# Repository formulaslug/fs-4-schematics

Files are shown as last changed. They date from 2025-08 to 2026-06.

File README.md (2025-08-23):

# Notes

Please complete KiCad training before beginning or working on any projects in this repository.

Only edit another person's work if you have spoke about it with them first and they have given you permission. This applies to Leads and Captains as well.

Contact Cole Lewis, Nathaniel Platt, or Wesley Rodriguez Kronmiller or Jack Nystrom for information/help relating to this repository.

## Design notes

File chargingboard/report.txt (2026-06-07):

Plotted to '/Users/mihirb/Desktop/formula slug/chargingboard.pdf'.
Info: Done.
Plotted to '/Users/mihirb/Desktop/formula slug/chargingboard.pdf'.
Info: Done.
Info: Done.
Info: Done.

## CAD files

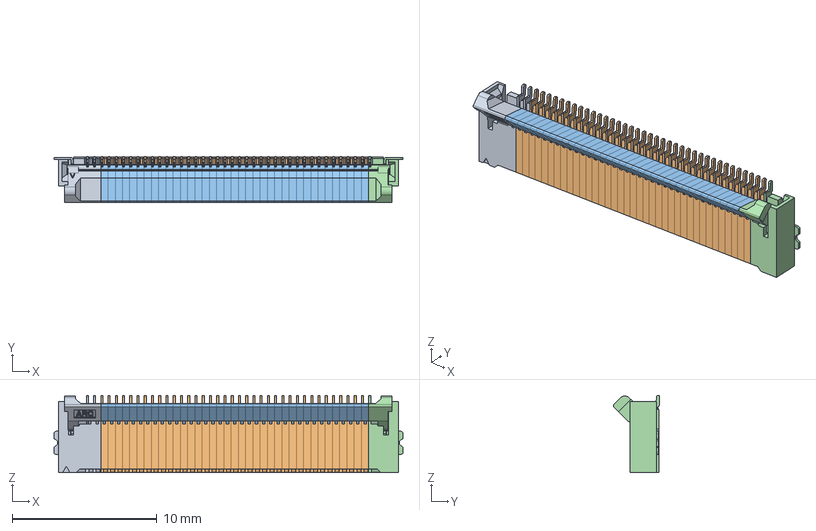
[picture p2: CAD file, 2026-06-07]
chargingboard/f32d_40pin_asm.stp
24.1 x 3.21 x 5.32 mm
F32D_L
F32D_M x 37
F32D_R

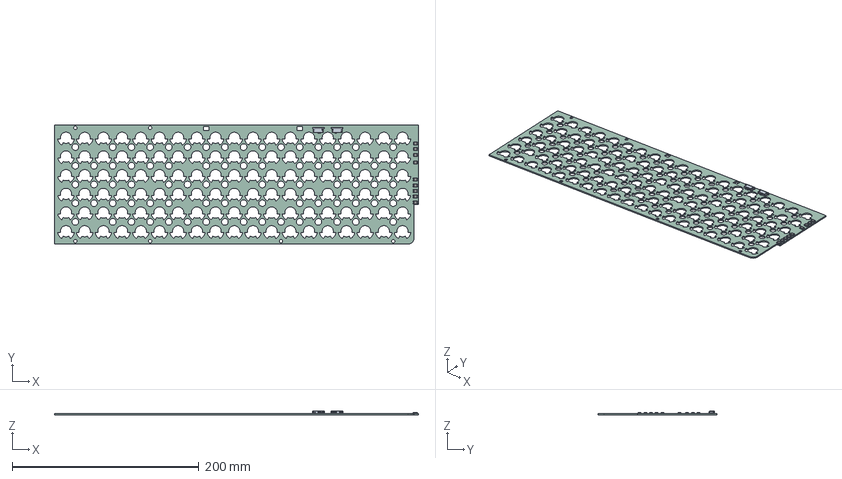
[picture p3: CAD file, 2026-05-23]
BMS Busbar Board/BMS Busbar Board/BMS Busbar Board.step
389.4 x 127.6 x 4.11 mm
1812L050_30PR x 9
BMS Busbar Board_PCB

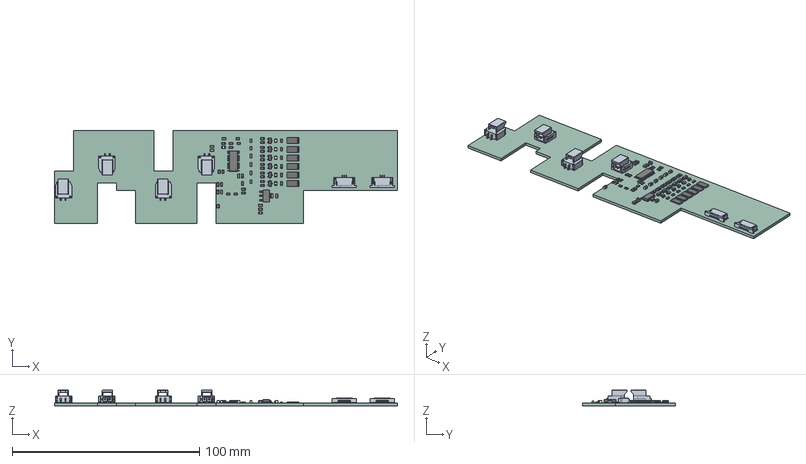
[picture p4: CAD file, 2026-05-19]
BMS/BMS/BMS.step
183.2 x 49.9 x 8.49 mm
R_0805_2012Metric x 35
C_0805_2012Metric x 14
LED_0805_2012Metric x 8
TSSOP-44_4.4x11mm_P0.5mm
R_2512_6332Metric x 6
SOT-223
SOT-23 x 6
BMS_PCB

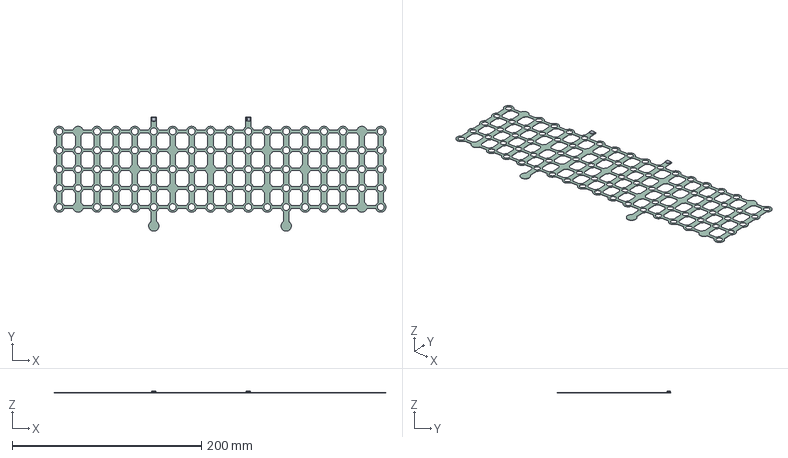
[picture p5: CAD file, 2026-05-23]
BMS/TempSenseBoard/TempSenseBoard.step
351.0 x 120.8 x 1.99 mm
TempSenseBoard_PCB

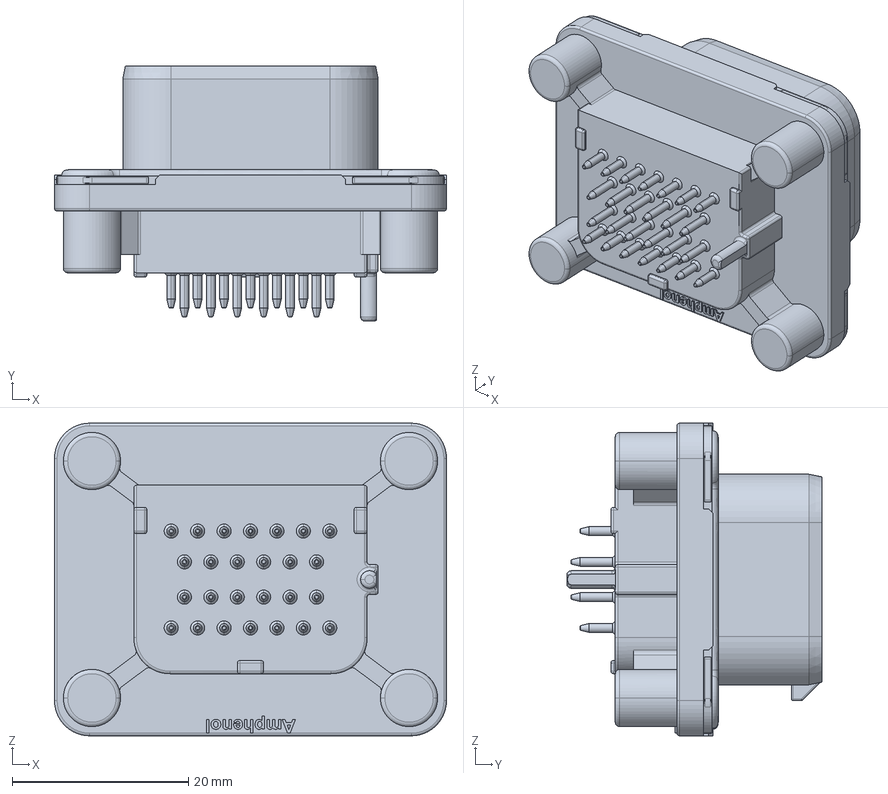
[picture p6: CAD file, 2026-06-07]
chargingboard/ATS15-26PB-BM01.stp
44.5 x 29.0 x 35.5 mm

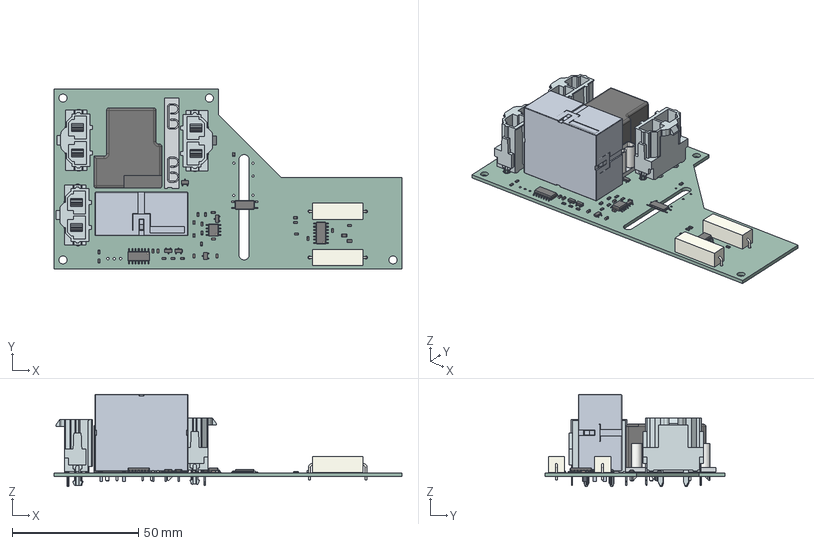
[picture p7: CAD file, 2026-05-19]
Power Electronics Board/Power Electronics Board.step
137.7 x 71.1 x 36.5 mm
SOIC-8_3.9x4.9mm_P1.27mm
TSOT-23 x 2
R_0603_1608Metric x 14
C_0603_1608Metric x 8
Pins
D_0603_1608Metric x 3
SOT-23-3 x 2
R_0805_2012Metric x 2
R_Axial_Power_L20.0mm_W6.4mm_P22.40mm x 2
SOIC-14_3.9x8.7mm_P1.27mm x 2
SOT-23
EW60-1A3-CL12D04,00000
SO-4_7.6x3.6mm_P2.54mm
Power Electronics Board_PCB

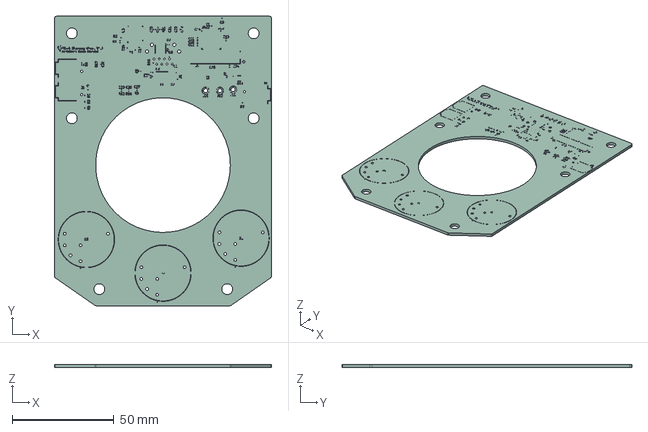
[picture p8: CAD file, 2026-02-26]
steering-wheel-board/steering_wheel.step
106.4 x 142.0 x 1.66 mm
steering_wheel_silkscreen x 2
steering_wheel_PCB

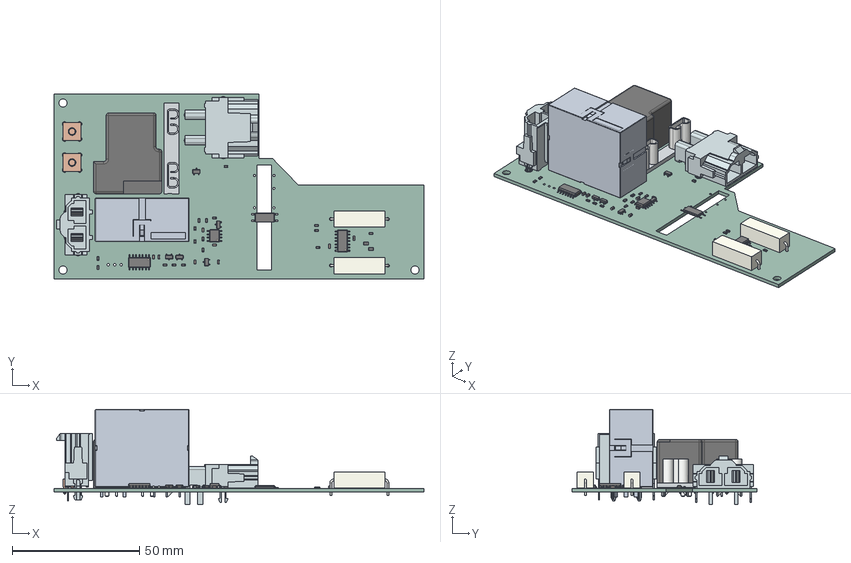
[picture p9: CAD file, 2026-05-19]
Power Electronics Board/Power Electronics Board V2.5.step
145.3 x 72.6 x 37.4 mm
SOIC-8_3.9x4.9mm_P1.27mm
TSOT-23 x 2
R_0603_1608Metric x 14
C_0603_1608Metric x 8
Pins
D_0603_1608Metric x 3
SOT-23-3 x 2
R_0805_2012Metric x 2
R_Axial_Power_L20.0mm_W6.4mm_P22.40mm x 2
SOIC-14_3.9x8.7mm_P1.27mm x 2
SOT-23
EW60-1A3-CL12D04,00000
74651173+(rev1) x 2
SO-4_7.6x3.6mm_P2.54mm
Power Electronics Board_PCB

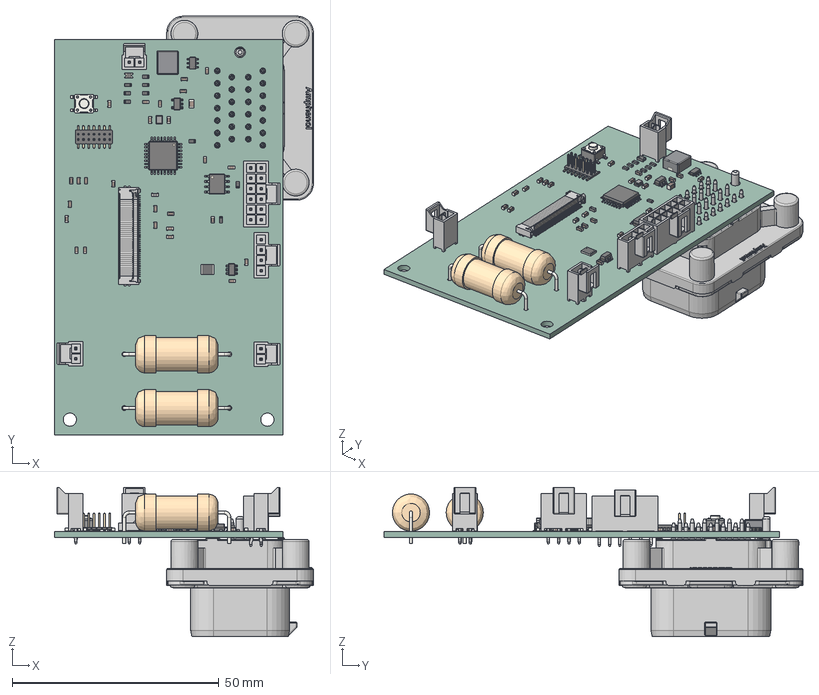
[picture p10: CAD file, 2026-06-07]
chargingboard/chargingboard.step
62.6 x 101.3 x 36.1 mm
C_0805_2012Metric
C_0603_1608Metric x 26
L_0603_1608Metric
PinHeader_2x07_P1.27mm_Vertical_SMD
SOT-23-6
R_1210_3225Metric
ATS15-26PB-BM01
D_0805_2012Metric
LQFP-32_7x7mm_P0.8mm
L_Bourns_SRP5030T
R_0603_1608Metric x 9
SOIC-8_3.9x4.9mm_P1.27mm
SOT-23-5
Crystal_SMD_2016-4Pin_2.0x1.6mm
TSOT-23-6
R_Axial_DIN0922_L20.0mm_D9.0mm_P25.40mm_Horizontal x 2
SW_SPST_PTS647Sx38
F32D_L
F32D_R
chargingboard_PCB

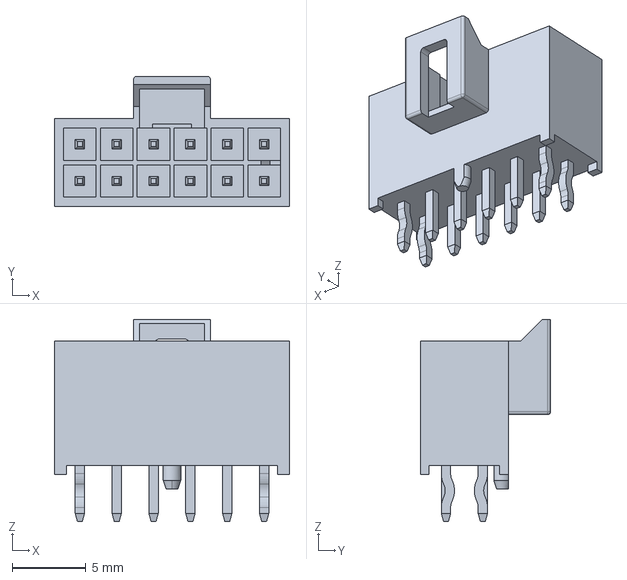
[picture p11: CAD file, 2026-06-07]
chargingboard/1053101112.stp
15.9 x 8.84 x 13.7 mm

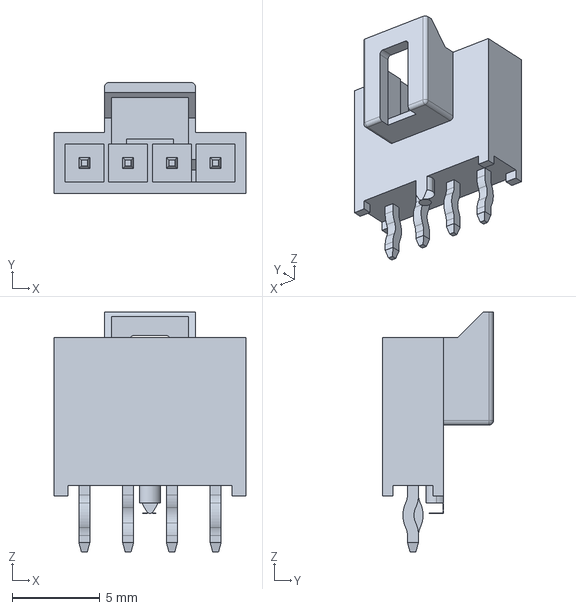
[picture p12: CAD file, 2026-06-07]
chargingboard/1053091204.stp
10.9 x 6.34 x 13.7 mm

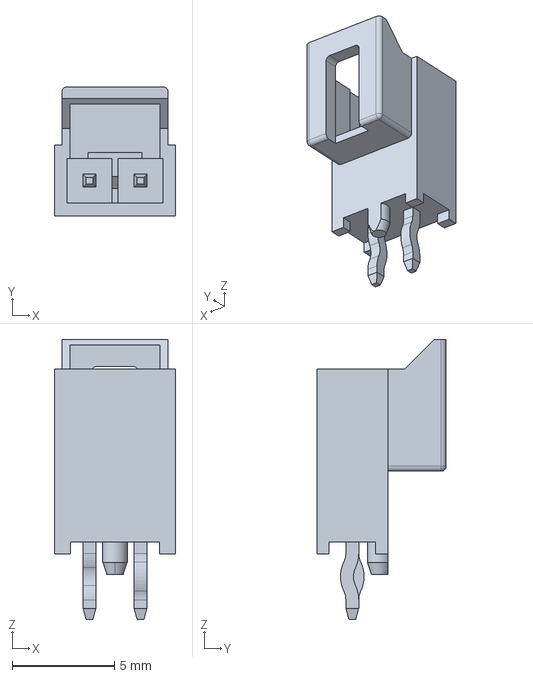
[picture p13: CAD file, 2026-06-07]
chargingboard/1053091102.stp
5.94 x 6.34 x 13.7 mm

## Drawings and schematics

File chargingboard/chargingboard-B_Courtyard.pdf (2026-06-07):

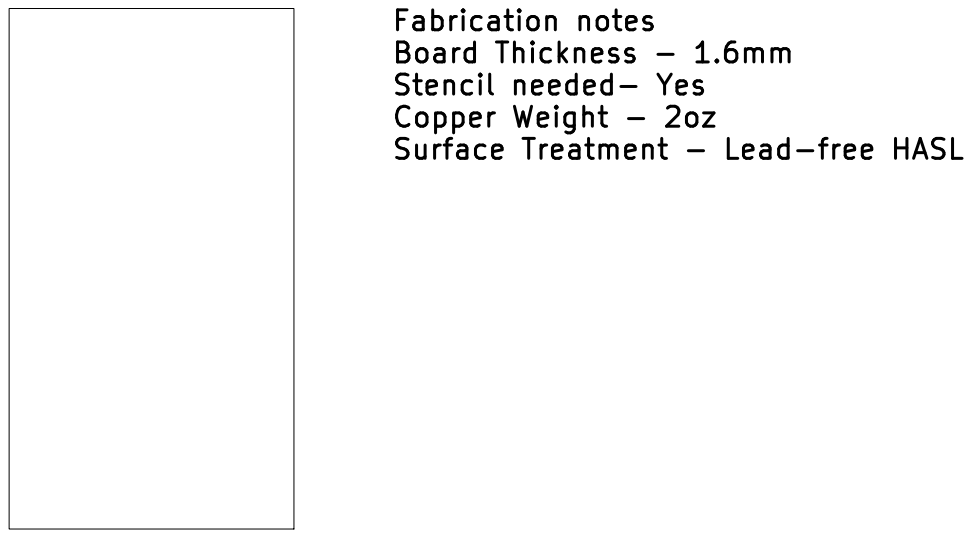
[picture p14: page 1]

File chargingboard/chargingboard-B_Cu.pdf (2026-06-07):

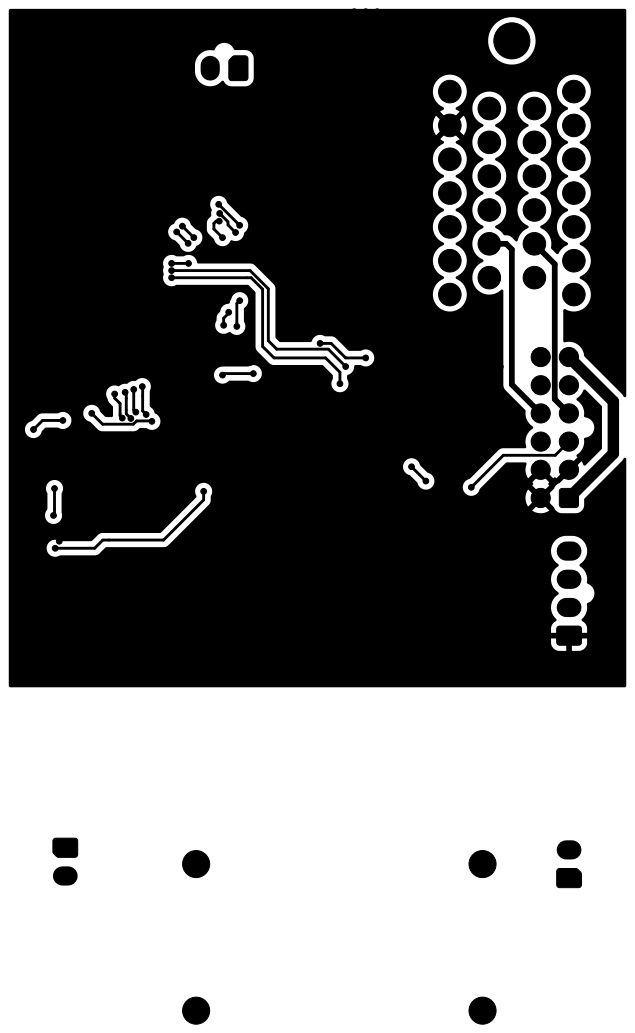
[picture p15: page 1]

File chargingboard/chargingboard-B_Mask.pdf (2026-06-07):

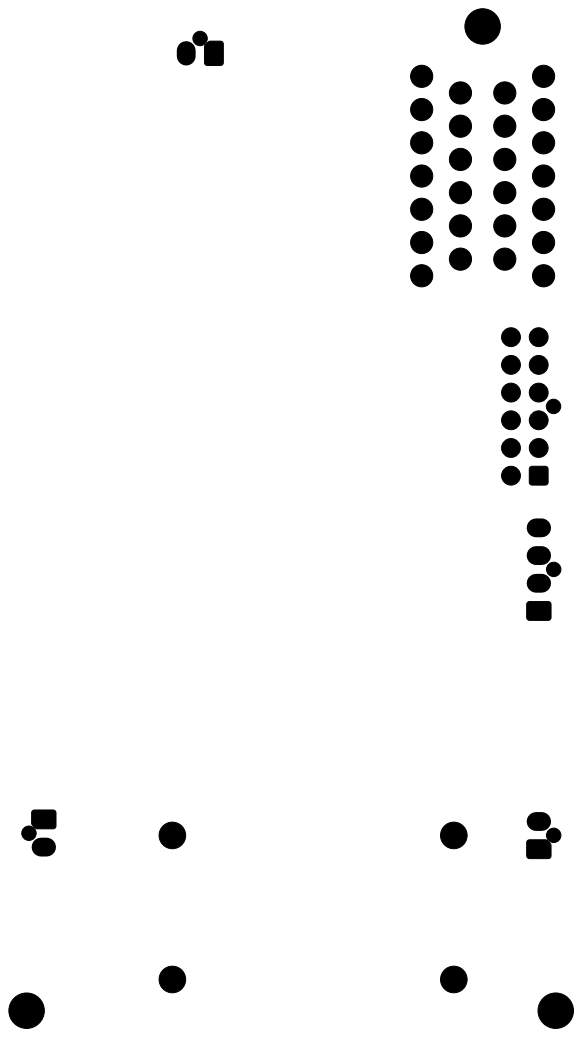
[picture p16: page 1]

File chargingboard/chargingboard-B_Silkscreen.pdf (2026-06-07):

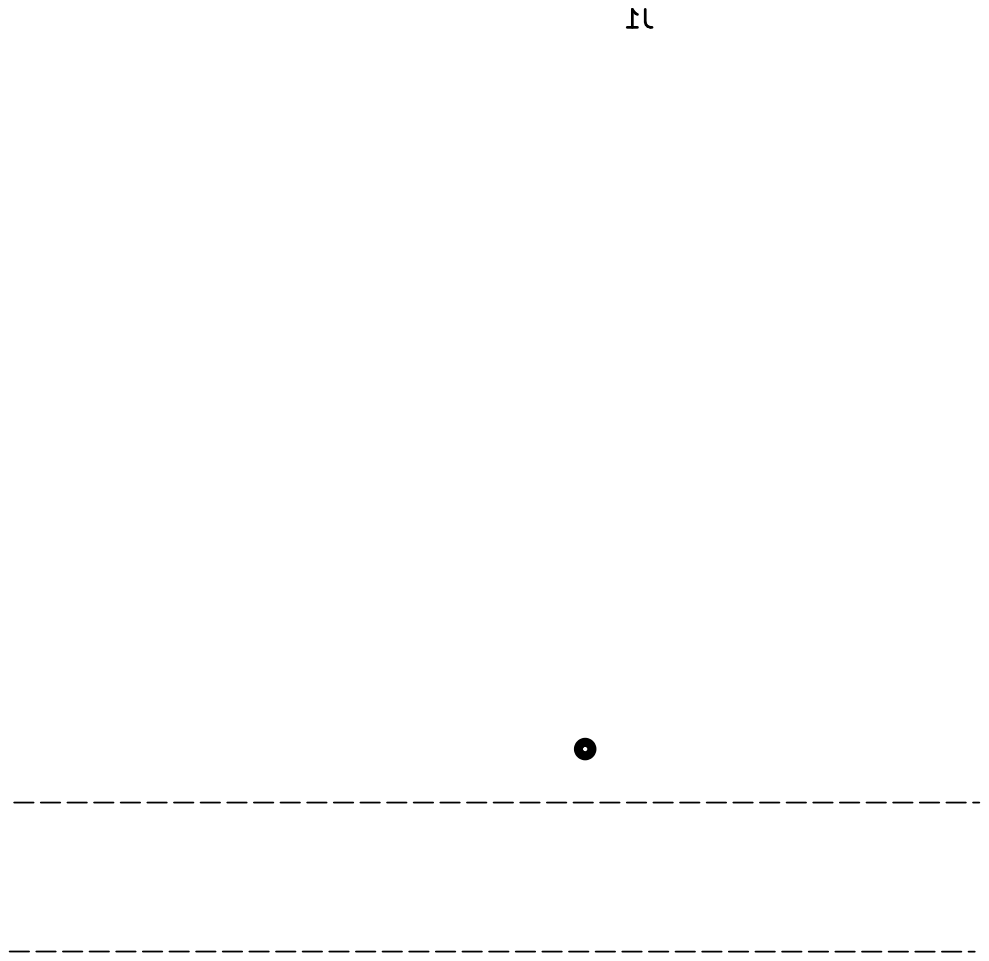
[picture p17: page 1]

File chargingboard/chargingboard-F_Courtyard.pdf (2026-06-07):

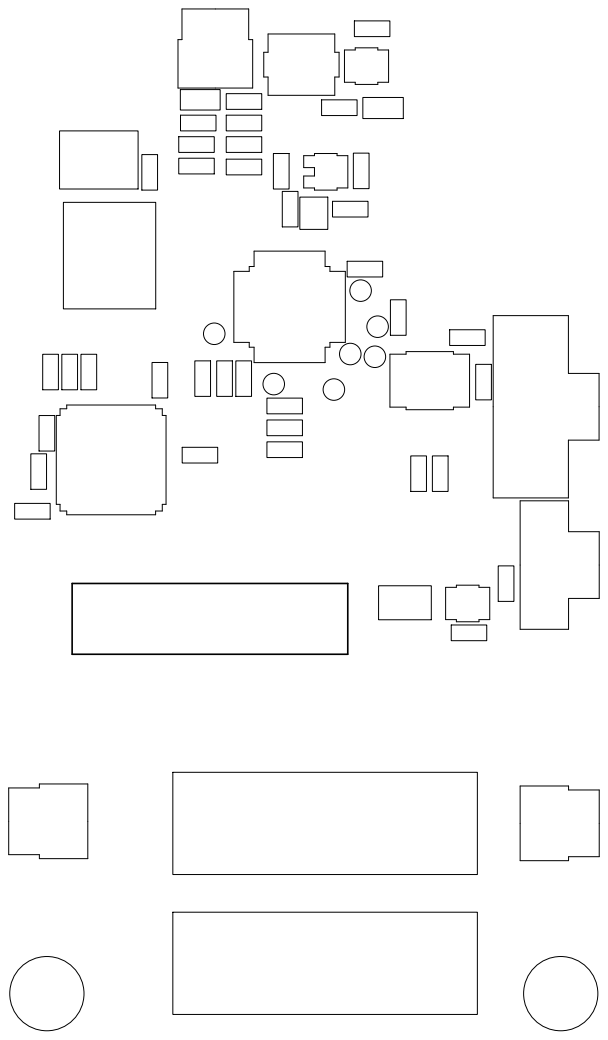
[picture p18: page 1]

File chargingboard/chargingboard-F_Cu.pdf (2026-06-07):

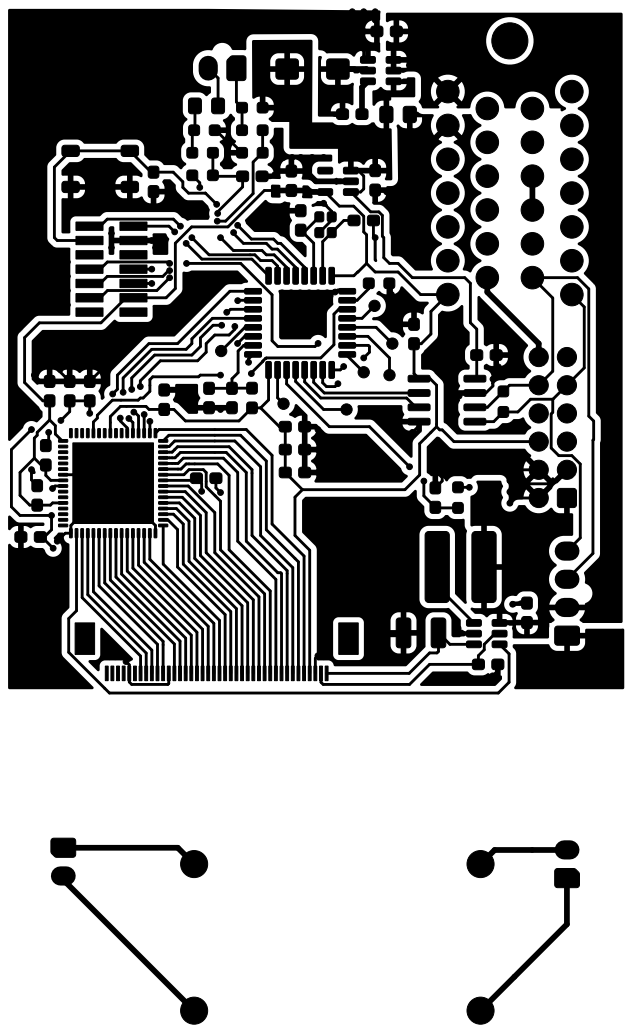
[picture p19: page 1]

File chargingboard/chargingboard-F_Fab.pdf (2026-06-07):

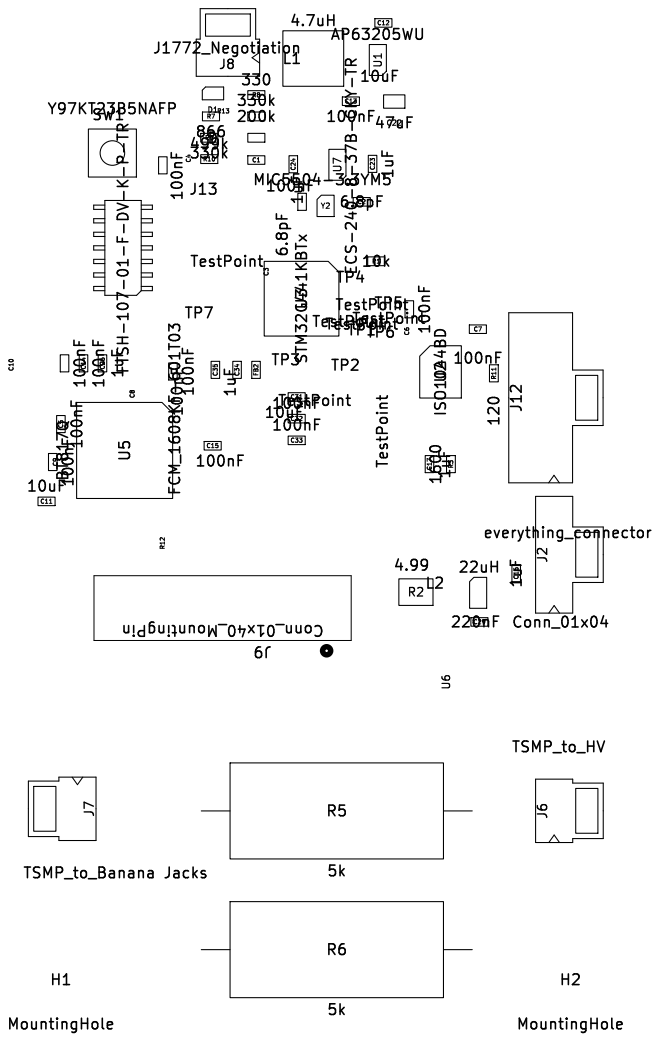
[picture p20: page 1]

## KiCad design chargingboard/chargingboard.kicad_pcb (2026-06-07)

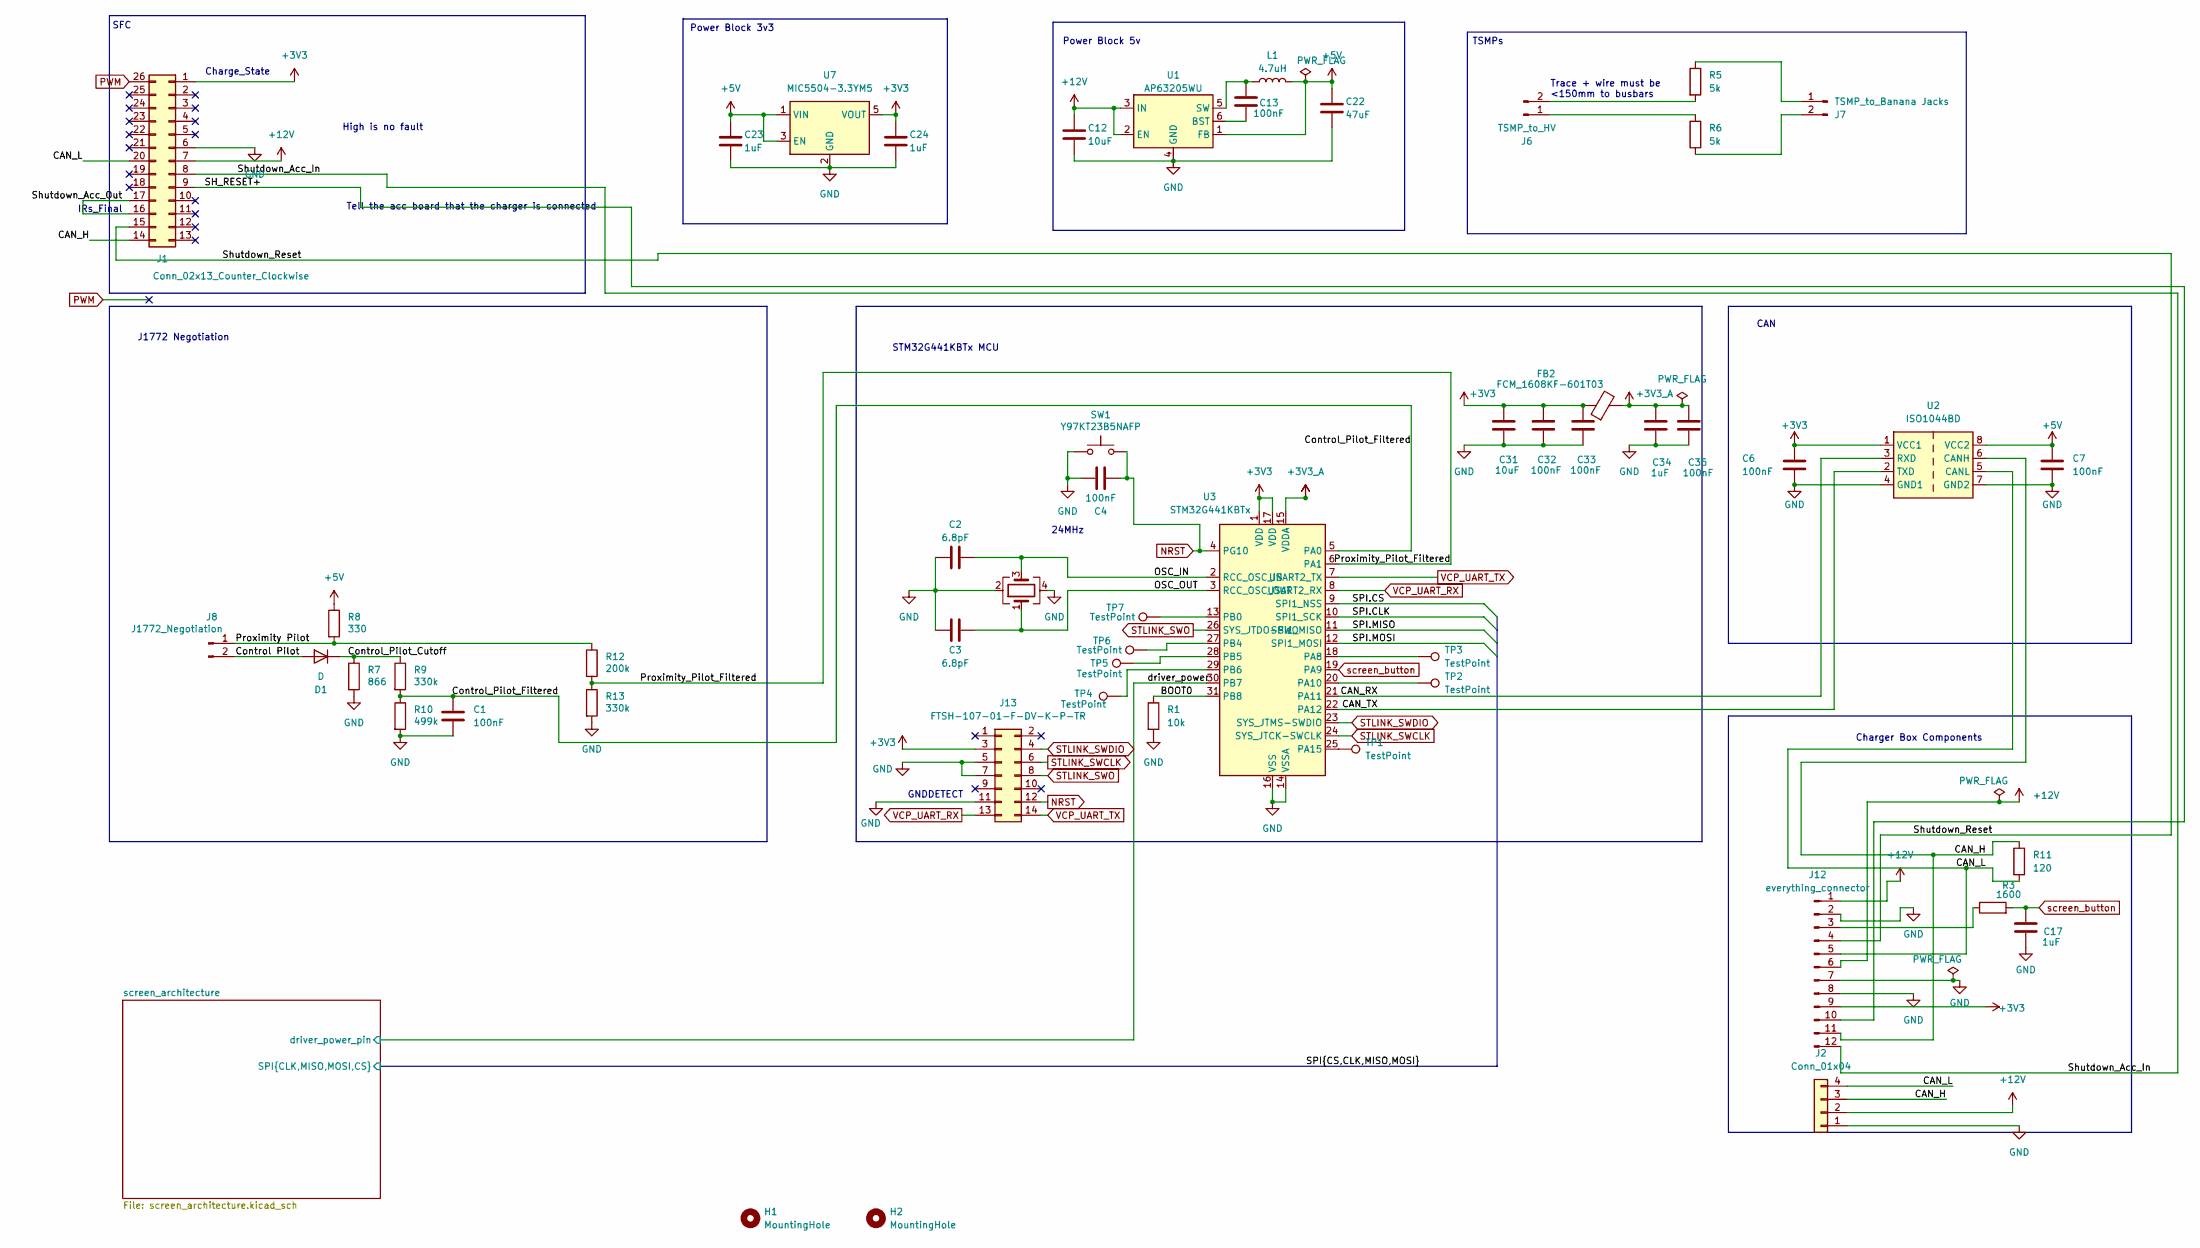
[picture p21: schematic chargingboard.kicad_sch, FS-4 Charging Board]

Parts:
C1, C4, C6, C7, C13, C32, C33, C35: 100nF; C_0603_1608Metric_Pad1.08x0.95mm_HandSolder; MFG PN CC0603KRX7R9BB104; Digi PN 311-1344-1-ND
C2, C3: 6.8pF; C_0603_1608Metric_Pad1.08x0.95mm_HandSolder; MFG PN CC0603DRNPO9BN6R8; Digi PN 311-3874-1-ND
C12, C31: 10uF; C_0603_1608Metric_Pad1.08x0.95mm_HandSolder; MFG PN CL10A106KO8NQNC; Digi PN 1276-CL10A106KO8NQNCCT-ND
C17, C23, C24, C34: 1uF; C_0603_1608Metric_Pad1.08x0.95mm_HandSolder; MFG PN CC0603KRX5R8BB105; Digi PN 311-1445-1-ND
C22: 47uF; C_0805_2012Metric_Pad1.18x1.45mm_HandSolder; MFG PN CL21A476MQYNNNE; Digi PN 1276-1852-1-ND
D1: D; D_0805_2012Metric_Pad1.15x1.40mm_HandSolder; MFG PN SMD110PL-TP; Digi PN SMD110PL-TPMSCT-ND
FB2: FCM_1608KF-601T03; L_0603_1608Metric_Pad1.05x0.95mm_HandSolder; MFG PN FCM1608KF-601T03; Digi PN 4816-FCM1608KF-601T03CT-ND
H1, H2: MountingHole; MountingHole_3.2mm_M3
J1: Conn_02x13_Counter_Clockwise; ATS15-26PB-BM01; MFG PN ATS15-26PB-BM01; Digi PN 889-ATS15-26PB-BM01-ND
J2: Conn_01x04; Molex_Nano-Fit_105309-xx04_1x04_P2.50mm_Vertical; MFG PN 1053091204; Digi PN WM14967-ND
J6: TSMP_to_HV; Molex_Nano-Fit_105309-xx02_1x02_P2.50mm_Vertical; MFG PN 1053091102; Digi PN WM16865-ND
J7: TSMP_to_Banana Jacks; Molex_Nano-Fit_105309-xx02_1x02_P2.50mm_Vertical; MFG PN 1053091102; Digi PN WM16865-ND
J8: J1772_Negotiation; Molex_Nano-Fit_105309-xx02_1x02_P2.50mm_Vertical; MFG PN 1053091102; Digi PN WM16865-ND
J12: everything_connector; Molex_Nano-Fit_105310-xx12_2x06_P2.50mm_Vertical; MFG PN 1053101112; Digi PN WM16883-ND
J13: FTSH-107-01-F-DV-K-P-TR; PinHeader_2x07_P1.27mm_Vertical_SMD; MFG PN FTSH-107-01-F-DV-K-P-TR; Digi PN SAM13170CT-ND
L1: 4.7uH; L_Bourns_SRP5030T; MFG PN SRP5030TA-4R7M; Digi PN SRP5030TA-4R7MCT-ND
R1: 10k; R_0603_1608Metric_Pad0.98x0.95mm_HandSolder; MFG PN AC0603FR-0710KL; Digi PN 311-10KLDCT-ND
R3: 1600; R_0603_1608Metric_Pad0.98x0.95mm_HandSolder; MFG PN RC0603FR-071K6L; Digi PN 311-1.60KHRCT-ND
R5, R6: 5k; R_Axial_DIN0922_L20.0mm_D9.0mm_P25.40mm_Horizontal; MFG PN WNE5K0FET; Digi PN WNE5K0FETCT-ND
R7: 866; R_0603_1608Metric_Pad0.98x0.95mm_HandSolder; MFG PN RMCF0603FT866R; Digi PN 738-RMCF0603FT866RCT-ND
R8: 330; R_0603_1608Metric_Pad0.98x0.95mm_HandSolder; MFG PN RC0603FR-07330RL; Digi PN 311-330HRCT-ND
R9, R13: 330k; R_0603_1608Metric_Pad0.98x0.95mm_HandSolder; MFG PN RMCF0603JT330K; Digi PN RMCF0603JT330KCT-ND
R10: 499k; R_0603_1608Metric_Pad0.98x0.95mm_HandSolder; MFG PN CRCW0603499KFKEA; Digi PN 541-499KHCT-ND
R11: 120; R_0603_1608Metric_Pad0.98x0.95mm_HandSolder; MFG PN ERA-3AEB121V; Digi PN P120DBCT-ND
R12: 200k; R_0603_1608Metric_Pad0.98x0.95mm_HandSolder; MFG PN ERA-3AEB204V; Digi PN P200KDBCT-ND
SW1: Y97KT23B5NAFP; SW_SPST_PTS647_Sx38; MFG PN Y97KT23B5NAFP; Digi PN 108-Y97KT23B5NAFPCT-ND
TP1, TP2, TP3, TP4, TP5, TP6, TP7: TestPoint; TestPoint_Pad_D1.0mm
U1: AP63205WU; TSOT-23-6; MFG PN AP63205WU-7; Digi PN AP63205WU-7DICT-ND
U2: ISO1044BD; SOIC-8_3.9x4.9mm_P1.27mm; MFG PN ISO1044BDR; Digi PN 296-ISO1044BDRCT-ND
U3: STM32G441KBTx; LQFP-32_7x7mm_P0.8mm; MFG PN STM32G441KBT6; Digi PN 497-STM32G441KBT6-ND
U7: MIC5504-3.3YM5; SOT-23-5; MFG PN MIC5504-3.3YM5-TR; Digi PN 576-4764-1-ND
Y2: ECS-240-8-37B-CKY-TR; Crystal_SMD_2016-4Pin_2.0x1.6mm; MFG PN ECS-240-8-37B-CKY-TR; Digi PN XC3063CT-ND

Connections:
+3V3: C6.1, C24.2, C31.2, C32.2, C33.2, FB2.1, J1.1, J12.9, J13.3, U2.1 (VCC1), U3.1 (VDD), U3.17 (VDD), U7.5 (VOUT); also elsewhere on the board
+3V3_A: C34.1, C35.1, FB2.2, U3.15 (VDDA)
+5V: C7.1, C22.2, C23.2, L1.2, R8.1, U1.1 (FB), U2.8 (VCC2), U7.1 (VIN), U7.3 (EN)
+12V: C12.2, J1.7, J2.2, J12.1, J12.6, U1.2 (EN), U1.3 (IN); also elsewhere on the board
/BOOT0: R1.1, U3.31 (PB8)
/CAN_H: J1.14, J2.3, J12.11, R11.1, U2.6 (CANH)
/CAN_L: J1.20, J2.4, J12.5, R11.2, U2.5 (CANL)
/CAN_RX: U2.3 (RXD), U3.21 (PA11)
/CAN_TX: U2.2 (TXD), U3.22 (PA12)
/Control Pilot: D1.2 (A), J8.2
/Control_Pilot_Cutoff: D1.1 (K), R7.1, R9.1
/Control_Pilot_Filtered: C1.1, R9.2, R10.1, U3.5 (PA0)
/OSC_IN: C2.1, U3.2 (RCC_OSC_IN), Y2.3
/OSC_OUT: C3.1, U3.3 (RCC_OSC_OUT), Y2.1
/Proximity Pilot: J8.1, R8.2, R12.1
/Proximity_Pilot_Filtered: R12.2, R13.1, U3.6 (PA1)
/SH_RESET+: J1.9, J12.10
/SPI.CLK: U3.10 (SPI1_SCK); also elsewhere on the board
/SPI.CS: U3.9 (SPI1_NSS); also elsewhere on the board
/SPI.MISO: U3.11 (SPI1_MISO); also elsewhere on the board
/SPI.MOSI: U3.12 (SPI1_MOSI); also elsewhere on the board
/Shutdown_Acc_In: J1.8, J12.12
/Shutdown_Acc_Out: J1.16, J1.17
/Shutdown_Reset: J1.15, J12.4
/driver_power: U3.30 (PB7); also elsewhere on the board
GND: C1.2, C2.2, C3.2, C4.1, C6.2, C7.2, C12.1, C17.2, C22.1, C23.1, C24.1, C31.1, C32.1, C33.1, C34.2, C35.2, J1.6, J2.1, J12.2, J12.7, J12.8, J13.5, J13.7, J13.11, R1.2, R7.2, R10.2, R13.2, SW1.1, U1.4 (GND), U2.4 (GND1), U2.7 (GND2), U3.14 (VSSA), U3.16 (VSS), U3.32 (VSS), U7.2 (GND), Y2.2, Y2.4; also elsewhere on the board
NRST: C4.2, J13.12, SW1.2, U3.4 (PG10)
unnamed: J6.1, R6.2
unnamed: J6.2, R5.2
unnamed: J7.1, R5.1
unnamed: J7.2, R6.1
unnamed: J12.3, R3.1
unnamed: C13.2, U1.6 (BST)
unnamed: C13.1, L1.1, U1.5 (SW)
unnamed: TP3.1, U3.18 (PA8)
unnamed: TP2.1, U3.20 (PA10)
unnamed: TP1.1, U3.25 (PA15)
unnamed: TP7.1, U3.13 (PB0)
unnamed: TP6.1, U3.27 (PB4)
unnamed: TP5.1, U3.28 (PB5)
unnamed: TP4.1, U3.29 (PB6)
PWM: J1.26
STLINK_SWCLK: J13.6, U3.24 (SYS_JTCK-SWCLK)
STLINK_SWDIO: J13.4, U3.23 (SYS_JTMS-SWDIO)
STLINK_SWO: J13.8, U3.26 (SYS_JTDO-SWO)
VCP_UART_RX: J13.13, U3.8 (USART2_RX)
VCP_UART_TX: J13.14, U3.7 (USART2_TX)
screen_button: C17.1, R3.2, U3.19 (PA9)

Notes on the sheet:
Trace + wire must be <150mm to busbars
STM32G441KBTx MCU
Tell the acc board that the charger is connected
CAN
GNDDETECT
J1772 Negotiation
SFC
Power Block 5v
High is no fault
TSMPs
Charger Box Components
Charge_State
Power Block 3v3
IRs_Final
24MHz

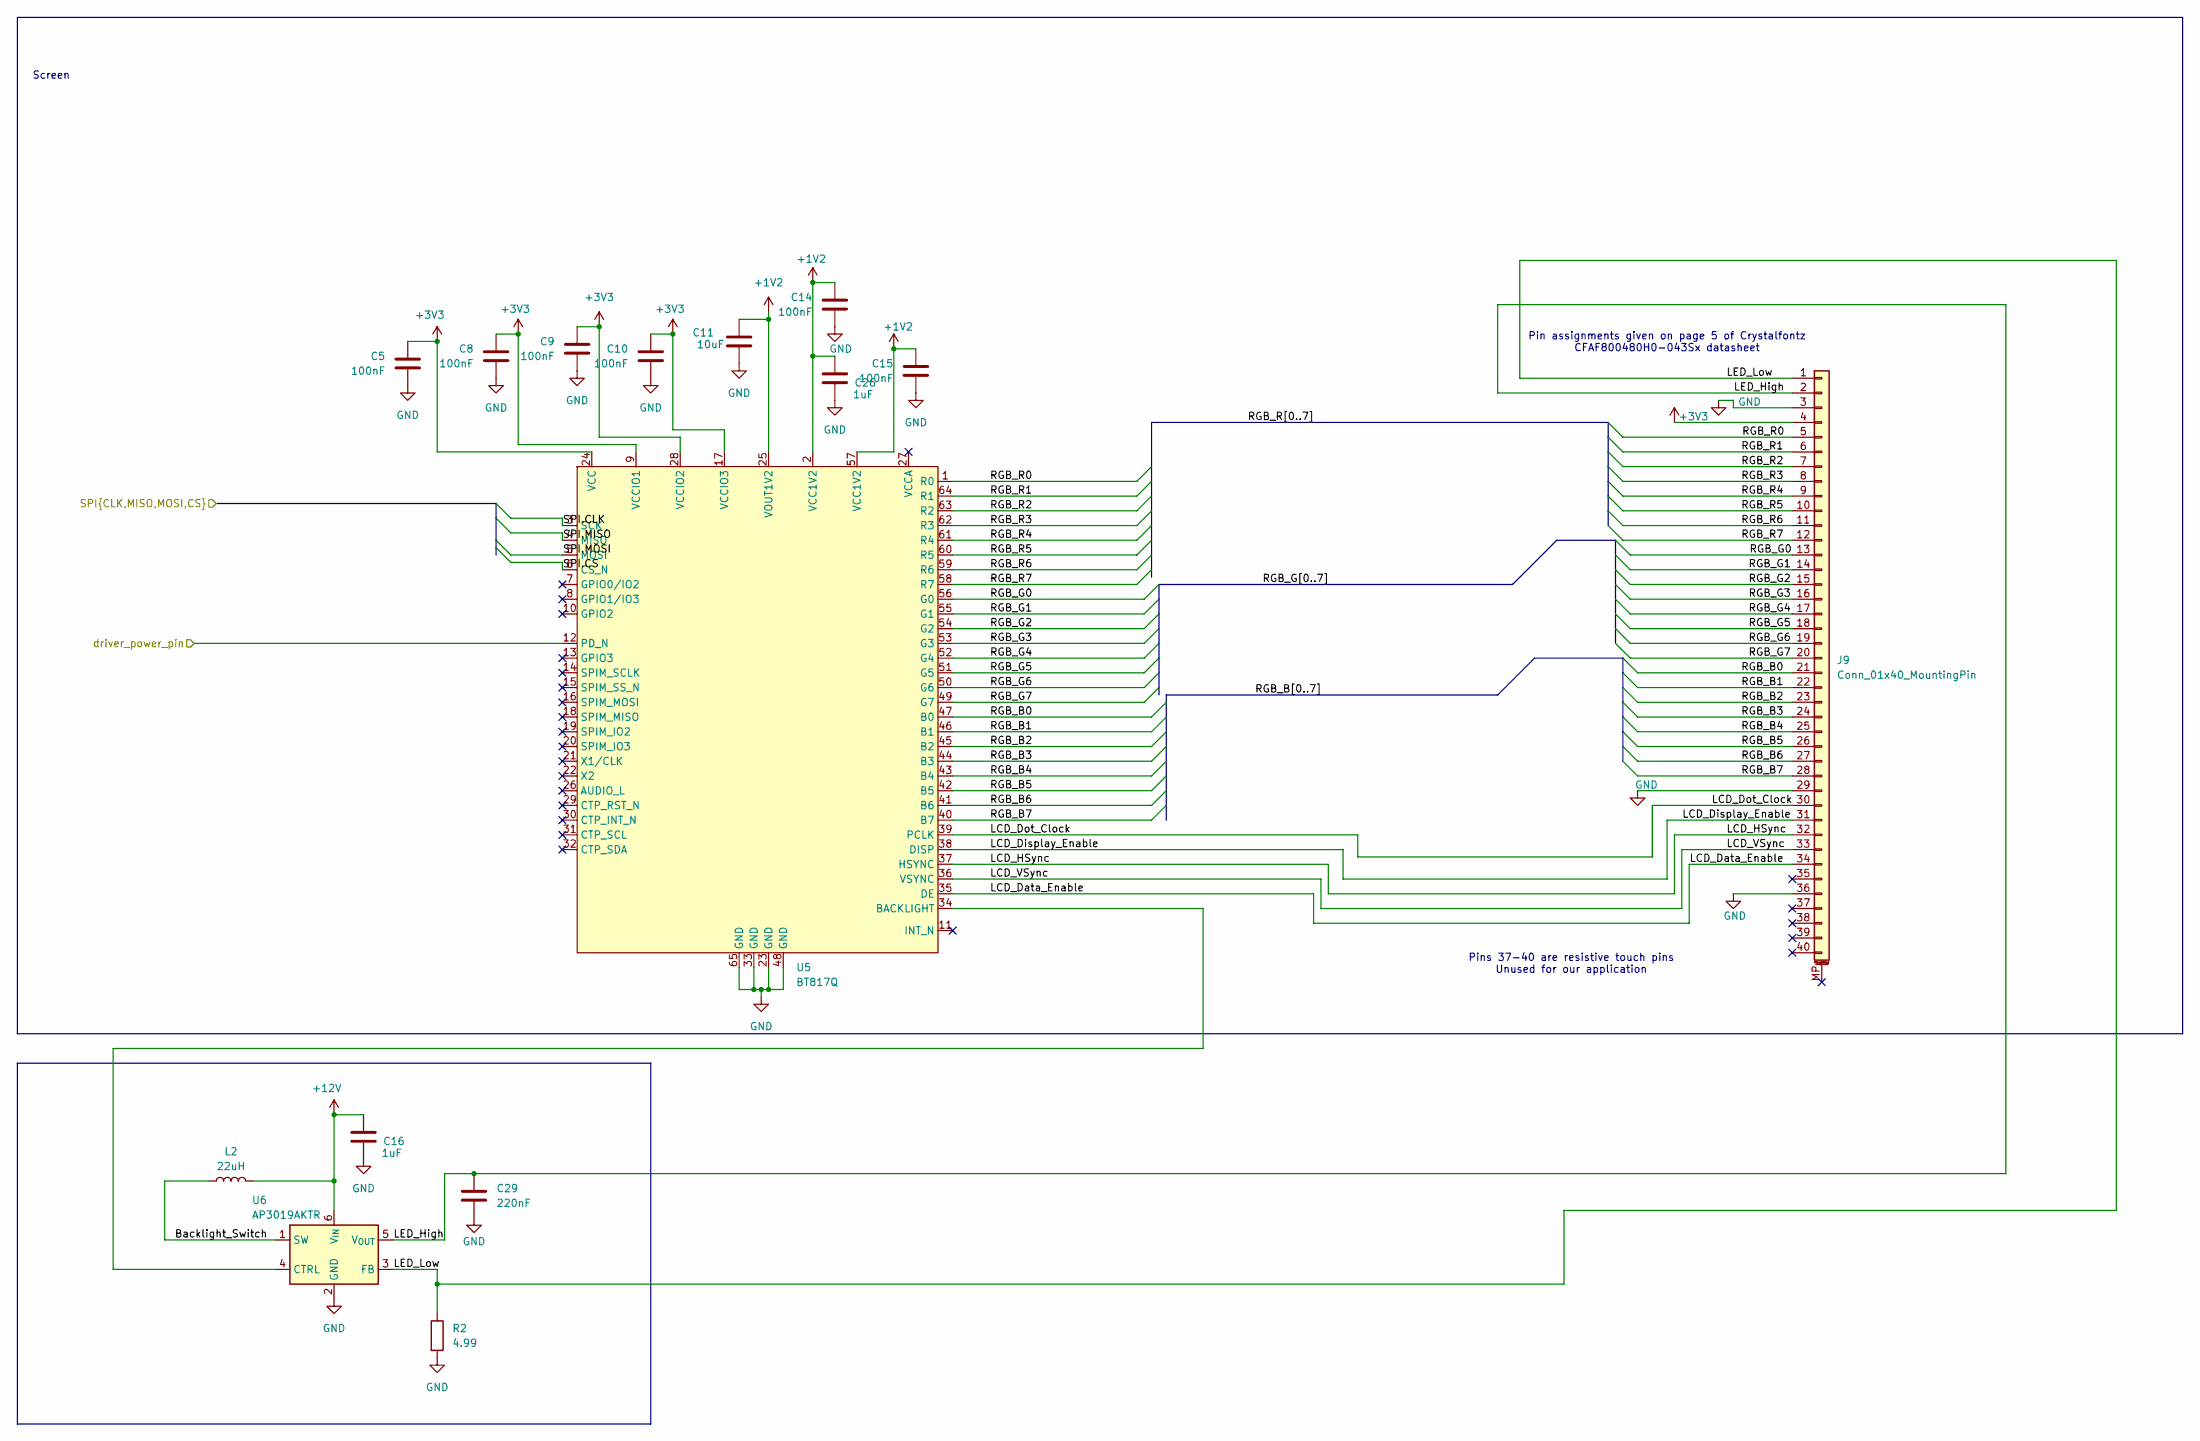
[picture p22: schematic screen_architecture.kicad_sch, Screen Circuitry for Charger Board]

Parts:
C5, C8, C9, C10, C14, C15: 100nF; C_0603_1608Metric_Pad1.08x0.95mm_HandSolder; MFG PN CC0603KRX7R9BB104; Digi PN 311-1344-1-ND
C11: 10uF; C_0603_1608Metric_Pad1.08x0.95mm_HandSolder; MFG PN CL10A106KO8NQNC; Digi PN 1276-CL10A106KO8NQNCCT-ND
C16, C26: 1uF; C_0603_1608Metric_Pad1.08x0.95mm_HandSolder; MFG PN CC0603KRX5R8BB105; Digi PN 311-1445-1-ND
C29: 220nF; C_0603_1608Metric_Pad1.08x0.95mm_HandSolder; MFG PN CC0603KRX7R8BB224; Digi PN 311-1803-1-ND
J9: Conn_01x40_MountingPin; CONN_F32D-1A7Y1-21040_AMP; MFG PN F32D-1A7Y1-21040; Digi PN 609-F32D-1A7Y1-21040CT-ND
L2: 22uH; CDRH5D28NP-220NC; MFG PN CDRH5D28NP-220NC; Digi PN 308-2307-1-ND
R2: 4.99; R_1210_3225Metric_Pad1.30x2.65mm_HandSolder; MFG PN RK73H2ETTD4R99F; Digi PN 2019-RK73H2ETTD4R99FCT-ND
U5: BT817Q; VQFN-64-1EP_9x9mm_P0.5mm_EP7.15x7.15mm; MFG PN BT817Q-R; Digi PN 2005-BT817Q-RCT-ND
U6: AP3019AKTR; SOT-23-6; MFG PN AP3019AKTR-G1; Digi PN AP3019AKTR-G1DICT-ND

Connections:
+1V2: C11.1, C14.1, C15.1, C26.1, U5.2 (VCC1V2), U5.25 (VOUT1V2), U5.57 (VCC1V2)
+3V3: C5.1, C8.1, C9.1, C10.1, J9.4, U5.9 (VCCIO1), U5.17 (VCCIO3), U5.24 (VCC), U5.28 (VCCIO2); also elsewhere on the board
+12V: C16.1, L2.2, U6.6 (V_{IN}); also elsewhere on the board
/SPI.CLK: U5.3 (SCK); also elsewhere on the board
/SPI.CS: U5.6 (CS_N); also elsewhere on the board
/SPI.MISO: U5.4 (MISO); also elsewhere on the board
/SPI.MOSI: U5.5 (MOSI); also elsewhere on the board
/driver_power: U5.12 (PD_N); also elsewhere on the board
/screen_architecture/Backlight_Switch: L2.1, U6.1 (SW)
/screen_architecture/LCD_Data_Enable: J9.34, U5.35 (DE)
/screen_architecture/LCD_Display_Enable: J9.31, U5.38 (DISP)
/screen_architecture/LCD_Dot_Clock: J9.30, U5.39 (PCLK)
/screen_architecture/LCD_HSync: J9.32, U5.37 (HSYNC)
/screen_architecture/LCD_VSync: J9.33, U5.36 (VSYNC)
/screen_architecture/LED_High: C29.1, J9.2, U6.5 (V_{OUT})
/screen_architecture/LED_Low: J9.1, R2.1, U6.3 (FB)
/screen_architecture/RGB_B0: J9.21, U5.47 (B0)
/screen_architecture/RGB_B1: J9.22, U5.46 (B1)
/screen_architecture/RGB_B2: J9.23, U5.45 (B2)
/screen_architecture/RGB_B3: J9.24, U5.44 (B3)
/screen_architecture/RGB_B4: J9.25, U5.43 (B4)
/screen_architecture/RGB_B5: J9.26, U5.42 (B5)
/screen_architecture/RGB_B6: J9.27, U5.41 (B6)
/screen_architecture/RGB_B7: J9.28, U5.40 (B7)
/screen_architecture/RGB_G0: J9.13, U5.56 (G0)
/screen_architecture/RGB_G1: J9.14, U5.55 (G1)
/screen_architecture/RGB_G2: J9.15, U5.54 (G2)
/screen_architecture/RGB_G3: J9.16, U5.53 (G3)
/screen_architecture/RGB_G4: J9.17, U5.52 (G4)
/screen_architecture/RGB_G5: J9.18, U5.51 (G5)
/screen_architecture/RGB_G6: J9.19, U5.50 (G6)
/screen_architecture/RGB_G7: J9.20, U5.49 (G7)
/screen_architecture/RGB_R0: J9.5, U5.1 (R0)
/screen_architecture/RGB_R1: J9.6, U5.64 (R1)
/screen_architecture/RGB_R2: J9.7, U5.63 (R2)
/screen_architecture/RGB_R3: J9.8, U5.62 (R3)
/screen_architecture/RGB_R4: J9.9, U5.61 (R4)
/screen_architecture/RGB_R5: J9.10, U5.60 (R5)
/screen_architecture/RGB_R6: J9.11, U5.59 (R6)
/screen_architecture/RGB_R7: J9.12, U5.58 (R7)
GND: C5.2, C8.2, C9.2, C10.2, C11.2, C14.2, C15.2, C16.2, C26.2, C29.2, J9.3, J9.29, J9.36, R2.2, U5.23 (GND), U5.33 (GND), U5.48 (GND), U5.65 (GND), U6.2 (GND); also elsewhere on the board
unnamed: U5.34 (BACKLIGHT), U6.4 (CTRL)

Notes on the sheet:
Pins 37-40 are resistive touch pins Unused for our application
Screen
Pin assignments given on page 5 of Crystalfontz CFAF800480H0-043Sx datasheet

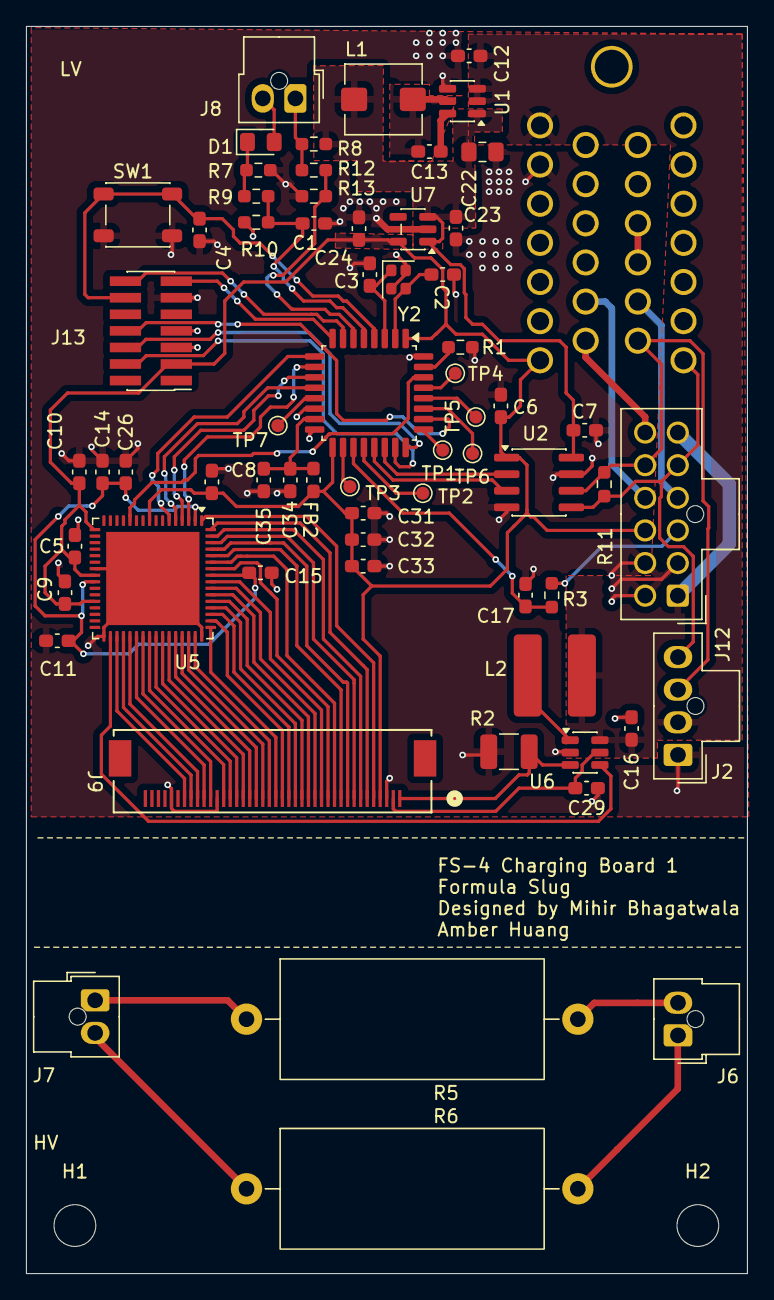
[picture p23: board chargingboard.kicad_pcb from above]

Board: 2 copper layers, 55.3 x 95.6 mm, 68 parts (1 on the bottom side), 81 nets.

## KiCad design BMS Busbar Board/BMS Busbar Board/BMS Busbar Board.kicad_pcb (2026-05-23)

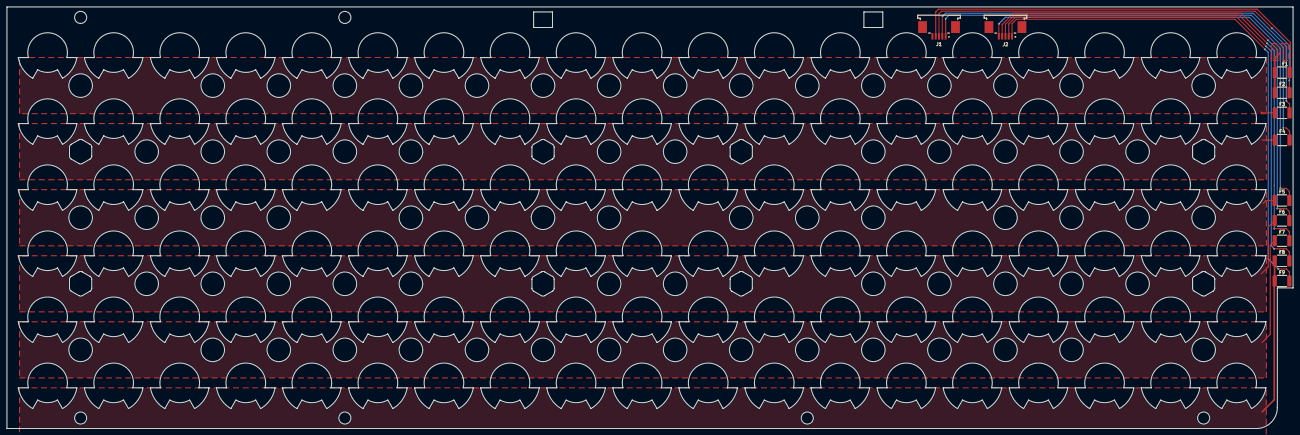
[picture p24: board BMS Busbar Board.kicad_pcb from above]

Board: 2 copper layers, 389.4 x 127.6 mm, 11 parts (0 on the bottom side), 11 nets.

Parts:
F1, F2, F3, F4, F5, F6, F7, F8, F9: Littlefuse 1812L050/30; Fuse_1812_4532Metric_Pad1.30x3.40mm_HandSolder
J1, J2: 84952-5; TE_84952-5

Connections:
/cell_0_minus: F8.1, F9.1
/cell_5_plus: F1.1, F2.1
/v_sense_cell_0: F7.2, J2.3
/v_sense_cell_1: F6.2, J2.4
/v_sense_cell_2: F5.2, J2.5
/v_sense_cell_3: F4.2, J1.1
/v_sense_cell_4: F3.2, J1.2
/v_sense_cell_5: F2.2, J1.3
/v_sense_minus: F8.2, J2.2
V_high: F1.2, J1.4
V_low: F9.2, J2.1

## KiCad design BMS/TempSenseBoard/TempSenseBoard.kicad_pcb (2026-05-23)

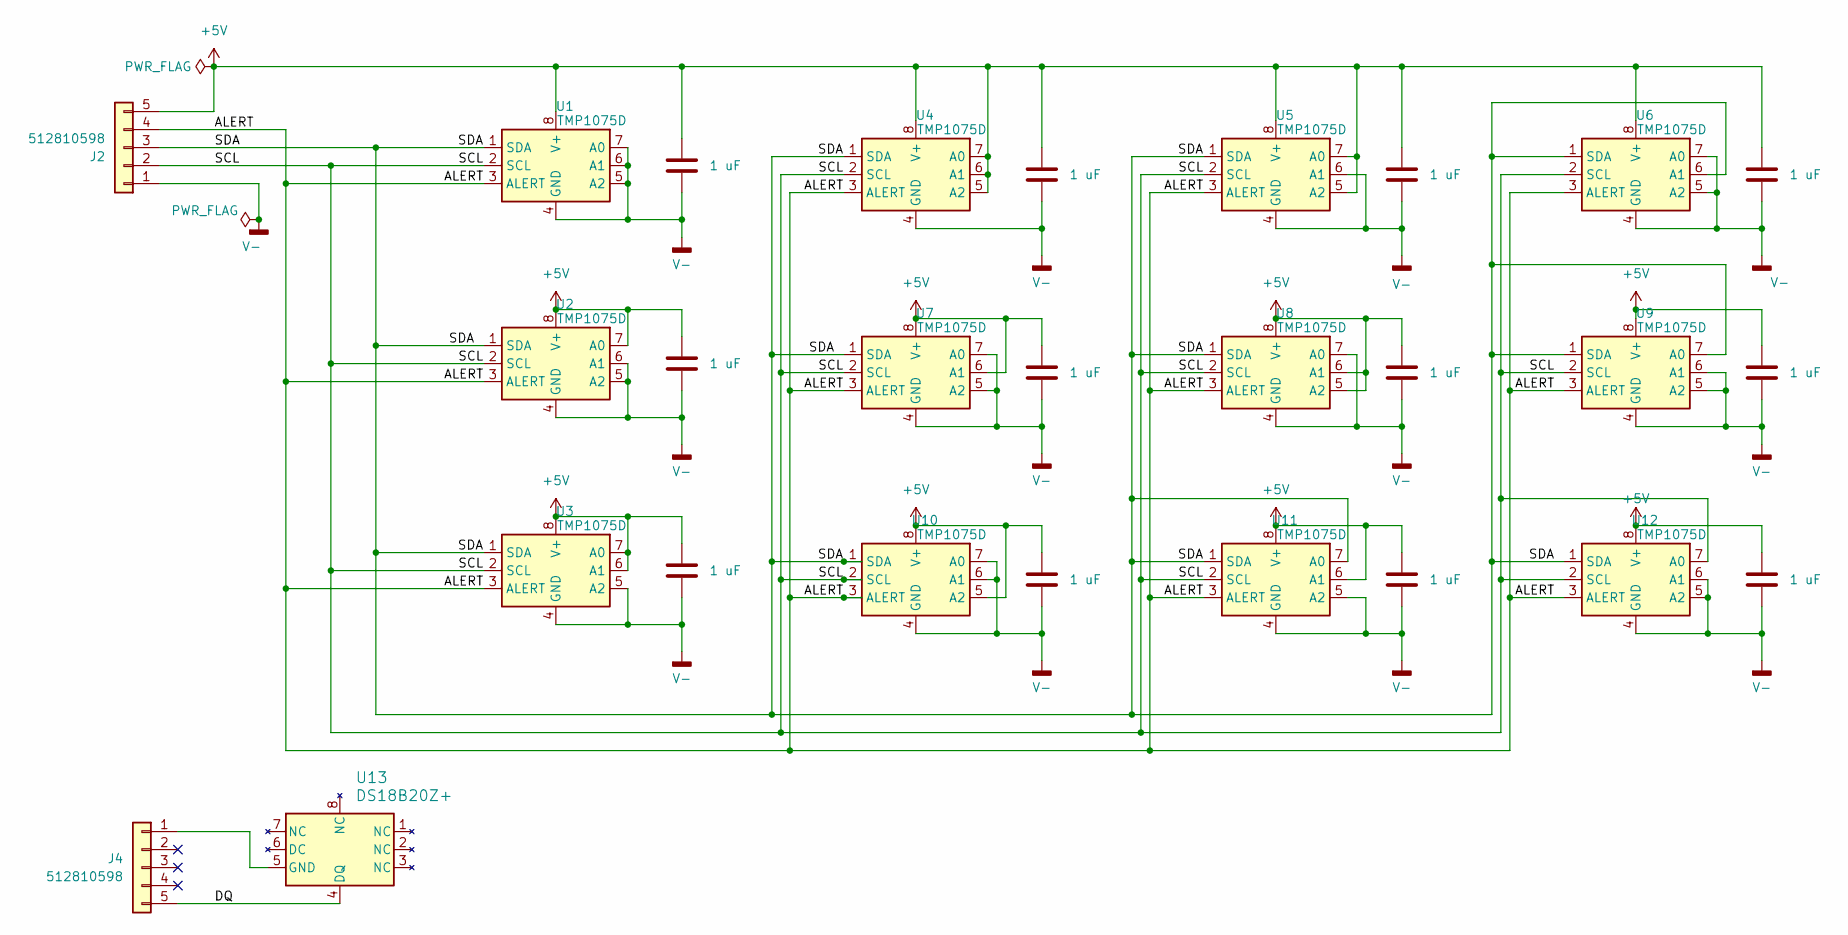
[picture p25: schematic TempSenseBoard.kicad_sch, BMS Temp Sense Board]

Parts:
C1, C2, C3, C4, C5, C6, C7, C8, C9, C10, C11, C12: 1 uF; C_0603_1608Metric_Pad1.08x0.95mm_HandSolder; MFG PN CC0603KRX5R8BB105; Digi PN 311-1445-1-ND
J2, J4: 512810598
U1, U2, U3, U4, U5, U6, U7, U8, U9, U10, U11, U12: TMP1075D; SO-8_3.9x4.9mm_P1.27mm; MFG PN TMP1075DR; Digi PN 296-51833-1-ND
U13: DS18B20Z+; 21-0041B_8_MXM; MFG PN DS18B20Z+; Digi PN DS18B20Z+-ND

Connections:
+5V: C1.1, C2.1, C3.1, C4.1, C5.1, C6.1, C7.1, C8.1, C9.1, C10.1, C11.1, C12.1, J2.5, U1.8 (V+), U2.7 (A0), U2.8 (V+), U3.6 (A1), U3.7 (A0), U3.8 (V+), U4.5 (A2), U4.6 (A1), U4.7 (A0), U4.8 (V+), U5.5 (A2), U5.7 (A0), U5.8 (V+), U6.8 (V+), U7.6 (A1), U7.8 (V+), U8.5 (A2), U8.6 (A1), U8.8 (V+), U9.8 (V+), U10.5 (A2), U10.8 (V+), U11.6 (A1), U11.8 (V+), U12.8 (V+)
/ALERT: J2.4, U1.3 (ALERT), U2.3 (ALERT), U3.3 (ALERT), U4.3 (ALERT), U5.3 (ALERT), U6.3 (ALERT), U7.3 (ALERT), U8.3 (ALERT), U9.3 (ALERT), U10.3 (ALERT), U11.3 (ALERT), U12.3 (ALERT)
/DQ: J4.5, U13.4 (DQ)
/SCL: J2.2, U1.2 (SCL), U2.2 (SCL), U3.2 (SCL), U4.2 (SCL), U5.2 (SCL), U6.2 (SCL), U7.2 (SCL), U8.2 (SCL), U9.2 (SCL), U10.2 (SCL), U11.2 (SCL), U12.2 (SCL), U12.7 (A0)
/SDA: J2.3, U1.1 (SDA), U2.1 (SDA), U3.1 (SDA), U4.1 (SDA), U5.1 (SDA), U6.1 (SDA), U6.6 (A1), U7.1 (SDA), U8.1 (SDA), U9.1 (SDA), U9.7 (A0), U10.1 (SDA), U11.1 (SDA), U11.7 (A0), U12.1 (SDA)
unnamed: J4.1, U13.5 (GND)
V-: C1.2, C2.2, C3.2, C4.2, C5.2, C6.2, C7.2, C8.2, C9.2, C10.2, C11.2, C12.2, J2.1, U1.4 (GND), U1.5 (A2), U1.6 (A1), U1.7 (A0), U2.4 (GND), U2.5 (A2), U2.6 (A1), U3.4 (GND), U3.5 (A2), U4.4 (GND), U5.4 (GND), U5.6 (A1), U6.4 (GND), U6.5 (A2), U6.7 (A0), U7.4 (GND), U7.5 (A2), U7.7 (A0), U8.4 (GND), U8.7 (A0), U9.4 (GND), U9.5 (A2), U9.6 (A1), U10.4 (GND), U10.6 (A1), U10.7 (A0), U11.4 (GND), U11.5 (A2), U12.4 (GND), U12.5 (A2), U12.6 (A1)

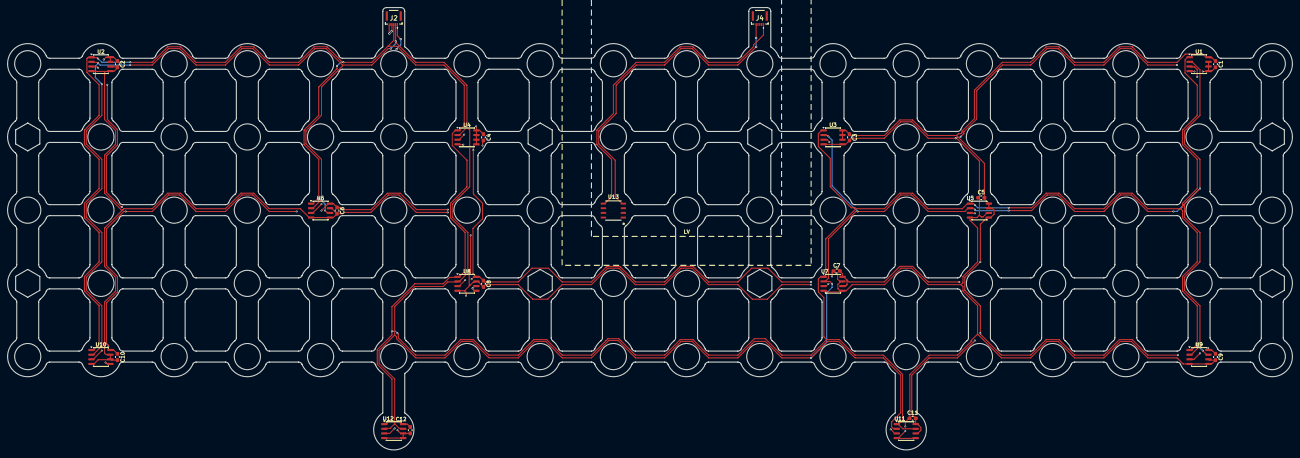
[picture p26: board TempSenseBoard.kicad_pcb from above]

Board: 4 copper layers, 351.0 x 120.8 mm, 27 parts (0 on the bottom side), 7 nets.

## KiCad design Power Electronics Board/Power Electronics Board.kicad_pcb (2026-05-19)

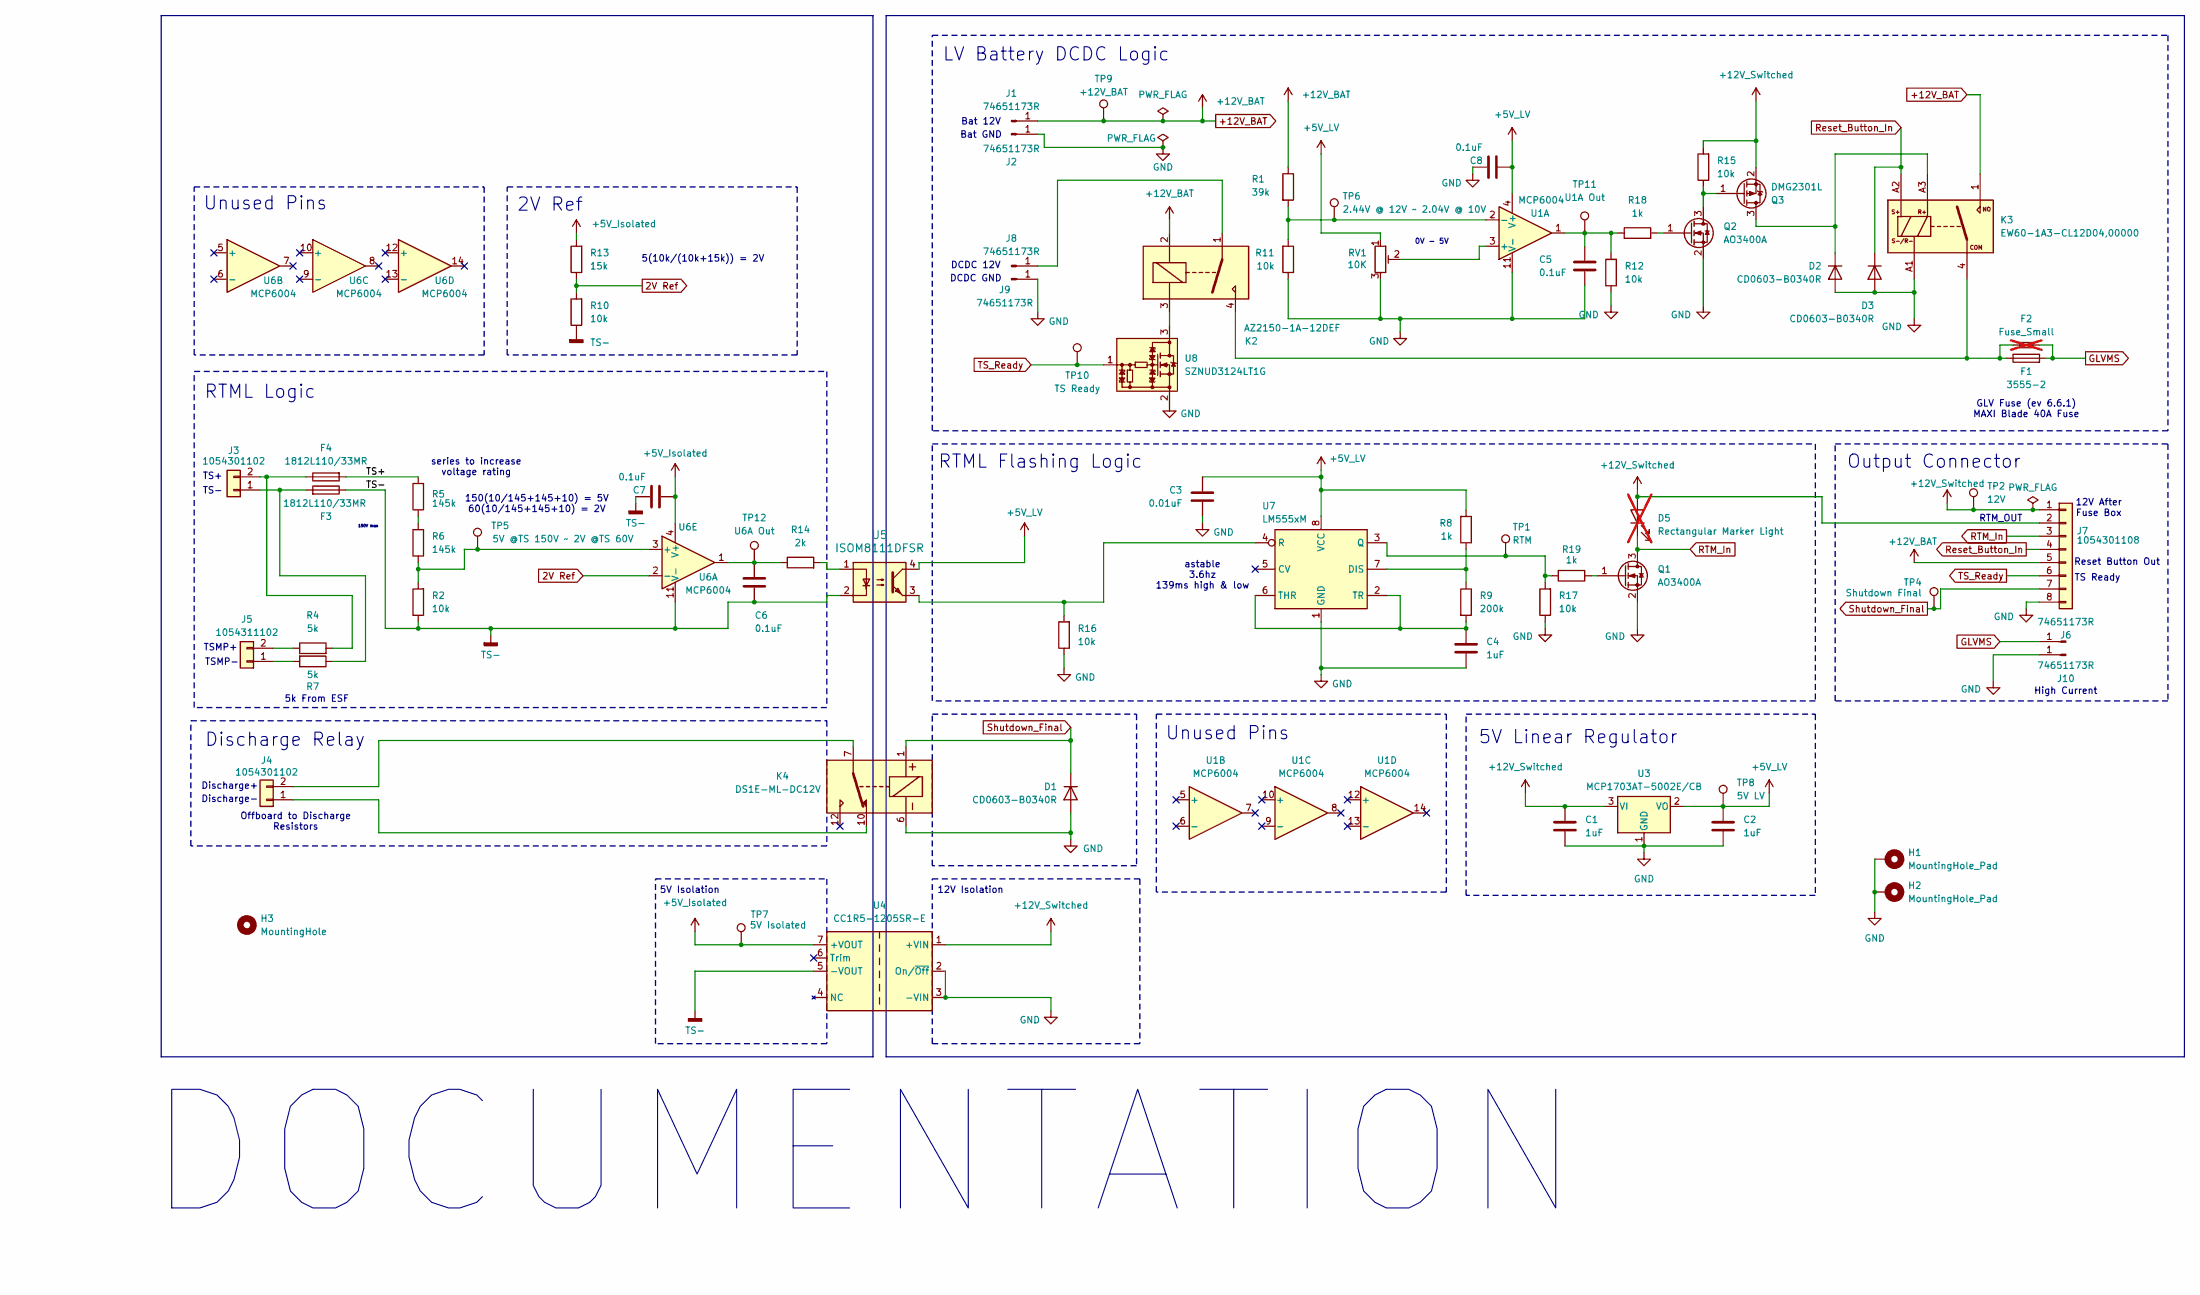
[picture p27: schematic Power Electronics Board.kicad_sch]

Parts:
C1, C2, C4: 1uF; C_0603_1608Metric_Pad1.08x0.95mm_HandSolder; MFG PN CL10B105KA8NNNC; Digi PN 1276-1184-1-ND
C3: 0.01uF; C_0603_1608Metric_Pad1.08x0.95mm_HandSolder; MFG PN CC0603KRX7R9BB103; Digi PN 311-1085-1-ND
C5, C6, C7, C8: 0.1uF; C_0603_1608Metric_Pad1.08x0.95mm_HandSolder; MFG PN CC0603KRX7R8BB104; Digi PN 311-1341-1-ND
D1, D2, D3: CD0603-B0340R; D_0603_1608Metric; MFG PN CD0603-B0340R; Digi PN CD0603-B0340RCT-ND
D5: Rectangular Marker Light; not fitted
F1: 3555-2; 3555-2_KEY; MFG PN 3555-2; Digi PN 36-3555-2-ND
F2: Fuse_Small; MFG PN 0299040.ZXNV; Digi PN F1037-ND; not fitted
F3, F4: 1812L110/33MR; Fuse_1812_4532Metric_Pad1.30x3.40mm_HandSolder; MFG PN 1812L110/33MR; Digi PN F3486CT-ND
H1, H2: MountingHole_Pad; MountingHole_3.2mm_M3_Pad
H3: MountingHole; MountingHole_3.2mm_M3
J1, J2, J6, J8, J9, J10: 74651173R; MFG PN 74651173R; Digi PN 732-74651173RCT-ND
J3, J4: 1054301102; CONN_SD-105430-001_02_MOL; MFG PN 1054301102; Digi PN WM26090CT-ND
J5: 1054311102; CONN_SD-105431-001_02_MOL; MFG PN 1054311102; Digi PN WM26073CT-ND
J7: 1054301108; Molex-Nano-Fit_2x04_SMD_Vertical; MFG PN 1054291208; Digi PN WM26116CT-ND
K2: AZ2150-1A-12DEF; AZ2150_AMZ; MFG PN AZ2150-1A-12DEF; Digi PN 3385-AZ2150-1A-12DEF-ND
K3: EW60-1A3-CL12D04,00000; EW601A3CL12D0400000; MFG PN EW60-1A3-CL12D04,00000; Digi PN PB2135-ND
K4: DS1E-ML-DC12V; MFG PN DS1E-ML-DC12V; Digi PN 255-2193-ND
Q1, Q2: AO3400A; SOT-23-3; MFG PN AO3400A; Digi PN 785-1000-1-ND
Q3: DMG2301L; SOT-23; MFG PN DMG2301L-13; Digi PN 31-DMG2301L-13CT-ND
R1: 39k; R_0603_1608Metric_Pad0.98x0.95mm_HandSolder; MFG PN RC0603FR-0739KL; Digi PN 311-39.0KHRCT-ND
R2, R10, R11, R12, R15, R16, R17: 10k; R_0603_1608Metric_Pad0.98x0.95mm_HandSolder; MFG PN RC0603FR-0710KL; Digi PN 311-10.0KHRCT-ND
R4, R7: 5k; R_Axial_Power_L20.0mm_W6.4mm_P22.40mm; MFG PN UB5C-5KF1; Digi PN 696-1085-ND
R5, R6: 145k; R_0805_2012Metric_Pad1.20x1.40mm_HandSolder; MFG PN RT0805BRD07145KL; Digi PN 13-RT0805BRD07145KLCT-ND
R8, R18, R19: 1k; R_0603_1608Metric_Pad0.98x0.95mm_HandSolder; MFG PN AC0603FR-071KL; Digi PN 311-1KLDCT-ND
R9: 200k; R_0603_1608Metric_Pad0.98x0.95mm_HandSolder; MFG PN RT0603BRD07200KL; Digi PN YAG1578CT-ND
R13: 15k; R_0603_1608Metric_Pad0.98x0.95mm_HandSolder; MFG PN RC0603FR-0715KL; Digi PN 311-15.0KHRCT-ND
R14: 2k; R_0603_1608Metric_Pad0.98x0.95mm_HandSolder; MFG PN AC0603FR-072KL; Digi PN YAG3590CT-ND
RV1: 10K; TRIM_PV36W103C01B00; MFG PN PV36W103C01B00; Digi PN 118-PV36W103C01B00-ND
TP1: RTM; TestPoint_Pad_1.0x1.0mm
TP2: 12V; TestPoint_Pad_1.0x1.0mm
TP4: Shutdown Final; TestPoint_Pad_1.0x1.0mm
TP5: 5V @TS 150V ~ 2V @TS 60V; TestPoint_Pad_1.0x1.0mm
TP6: 2.44V @ 12V ~ 2.04V @ 10V; TestPoint_Pad_1.0x1.0mm
TP7: 5V Isolated; TestPoint_Pad_1.0x1.0mm
TP8: 5V LV; TestPoint_Pad_1.0x1.0mm
TP9: +12V_BAT; TestPoint_Pad_1.0x1.0mm
TP10: TS Ready; TestPoint_Pad_1.0x1.0mm
TP11: U1A Out; TestPoint_Pad_1.0x1.0mm
TP12: U6A Out; TestPoint_Pad_1.0x1.0mm
U1, U6: MCP6004; SOIC-14_3.9x8.7mm_P1.27mm; MFG PN MCP6004-I/SL; Digi PN MCP6004-I/SL-ND
U3: MCP1703AT-5002E/CB; TSOT-23_HandSoldering; MFG PN MCP1703AT-5002E/CB; Digi PN MCP1703AT-5002E/CBCT-ND
U4: CC1R5-1205SR-E; MFG PN CC1R5-1205SR-E; Digi PN 445-2453-ND
U5: ISOM8111DFSR; SO-4_7.6x3.6mm_P2.54mm; MFG PN ISOM8111DFSR; Digi PN 296-ISOM8111DFSRCT-ND
U7: LM555xM; SOIC-8_3.9x4.9mm_P1.27mm; MFG PN LM555CMX/NOPB; Digi PN LM555CMX/NOPBCT-ND
U8: SZNUD3124LT1G; TSOT-23_HandSoldering; MFG PN SZNUD3124LT1G; Digi PN SZNUD3124LT1GOSCT-ND

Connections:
2V Ref: R10.2, R13.1, U6.2 (-)
+5V_Isolated: C7.2, R13.2, TP7.1, U4.7 (+VOUT), U6.4 (V+)
+5V_LV: C2.1, C3.1, C8.2, R8.2, RV1.1, TP8.1, U1.4 (V+), U3.2 (VO), U5.4, U7.8 (VCC)
+12V_BAT: J1.1, J7.5, K2.2, K3.1 (NO_1), K3.2 (NO_2), K3.3 (NO_3), R1.1, TP9.1
+12V_Switched: C1.1, D5.2 (A), J7.1, J7.2, Q3.2 (S), R15.2, TP2.1, U3.3 (VI), U4.1 (+VIN)
/TS+: F4.2, R5.2
GLVMS: F1.3, F1.4, F2.2, J6.1
GND: C1.2, C2.2, C3.2, C4.2, C5.2, C8.1, D1.2 (A), D2.2 (A), D3.2 (A), H1.1, H2.1, J2.1, J7.8, J9.1, J10.1, K3.A1 (S-/R-), K4.6, Q1.2 (S), Q2.2 (S), R11.1, R12.1, R16.1, R17.1, RV1.3, U1.11 (V-), U3.1 (GND), U4.2 (On/~Off), U4.3 (-VIN), U7.1 (GND), U8.2
unnamed: C5.1, R12.2, R18.1, TP11.1, U1.1
unnamed: C6.1, R14.1, TP12.1, U6.1
unnamed: D2.1 (K), K3.A3 (R+), Q3.3 (D)
unnamed: F3.2, J3.1, R7.1
unnamed: F4.1, J3.2, R4.2
unnamed: J4.1, K4.10
unnamed: J4.2, K4.7
unnamed: J5.1, R7.2
unnamed: J5.2, R4.1
unnamed: J8.1, K2.1
unnamed: K2.3, U8.3
unnamed: F1.1, F1.2, F2.1, K2.4, K3.4 (COM_1), K3.5 (COM_2), K3.6 (COM_3)
unnamed: Q1.1 (G), R19.1
unnamed: Q2.3 (D), Q3.1 (G), R15.1
unnamed: Q2.1 (G), R18.2
unnamed: R5.1, R6.2
unnamed: R14.2, U5.1
unnamed: RV1.2, U1.3 (+)
unnamed: R1.2, R11.2, TP6.1, U1.2 (-)
unnamed: R2.2, R6.1, TP5.1, U6.3 (+)
unnamed: R8.1, R9.1, U7.7 (DIS)
unnamed: R17.2, R19.2, TP1.1, U7.3 (Q)
unnamed: R16.2, U5.3, U7.4 (R)
unnamed: C4.1, R9.2, U7.2 (TR), U7.6 (THR)
RTM_In: D5.1 (K), J7.3, Q1.3 (D)
Reset_Button_In: D3.1 (K), J7.4, K3.A2 (S+)
Shutdown_Final: D1.1 (K), J7.7, K4.1, TP4.1
TS-: C6.2, C7.1, F3.1, R2.1, R10.1, U4.5 (-VOUT), U5.2, U6.11 (V-)
TS_Ready: J7.6, TP10.1, U8.1

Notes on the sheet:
Discharge-
DCDC GND
Reset Button Out
Bat GND
Unused Pins
5k From ESF
RTML Logic
150V max
High Current
TS-
RTM_OUT
RTML Flashing Logic
Output Connector
12V After Fuse Box
TS Ready
GLV Fuse (ev 6.6.1) MAXI Blade 40A Fuse
12V Isolation
150(10/145+145+10) = 5V 60(10/145+145+10) = 2V
5V Linear Regulator
series to increase voltage rating
Offboard to Discharge Resistors
DOCUMENTATION
Discharge+
Bat 12V
LV Battery DCDC Logic
0V - 5V
TSMP-
Discharge Relay
TS+
2V Ref
astable 3.6hz 139ms high & low
DCDC 12V
5V Isolation
TSMP+
5(10k/(10k+15k)) = 2V

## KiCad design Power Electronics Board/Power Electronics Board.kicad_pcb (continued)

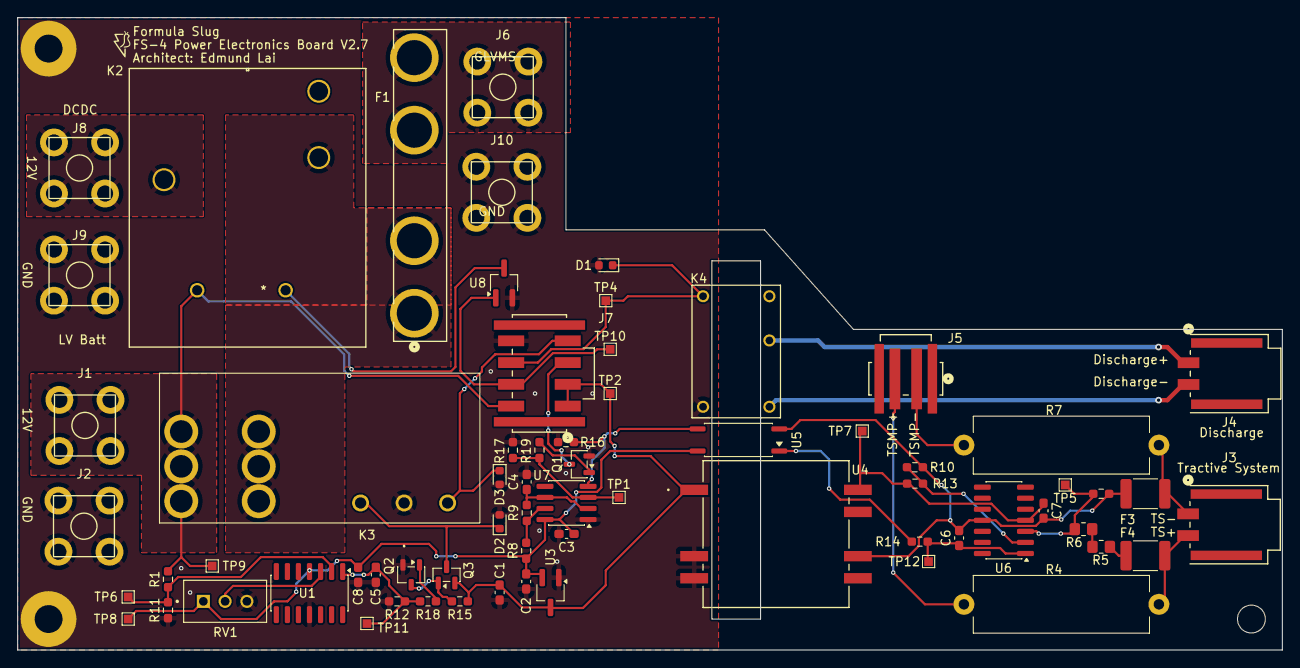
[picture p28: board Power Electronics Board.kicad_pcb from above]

Board: 2 copper layers, 145.3 x 72.6 mm, 70 parts (0 on the bottom side), 37 nets.

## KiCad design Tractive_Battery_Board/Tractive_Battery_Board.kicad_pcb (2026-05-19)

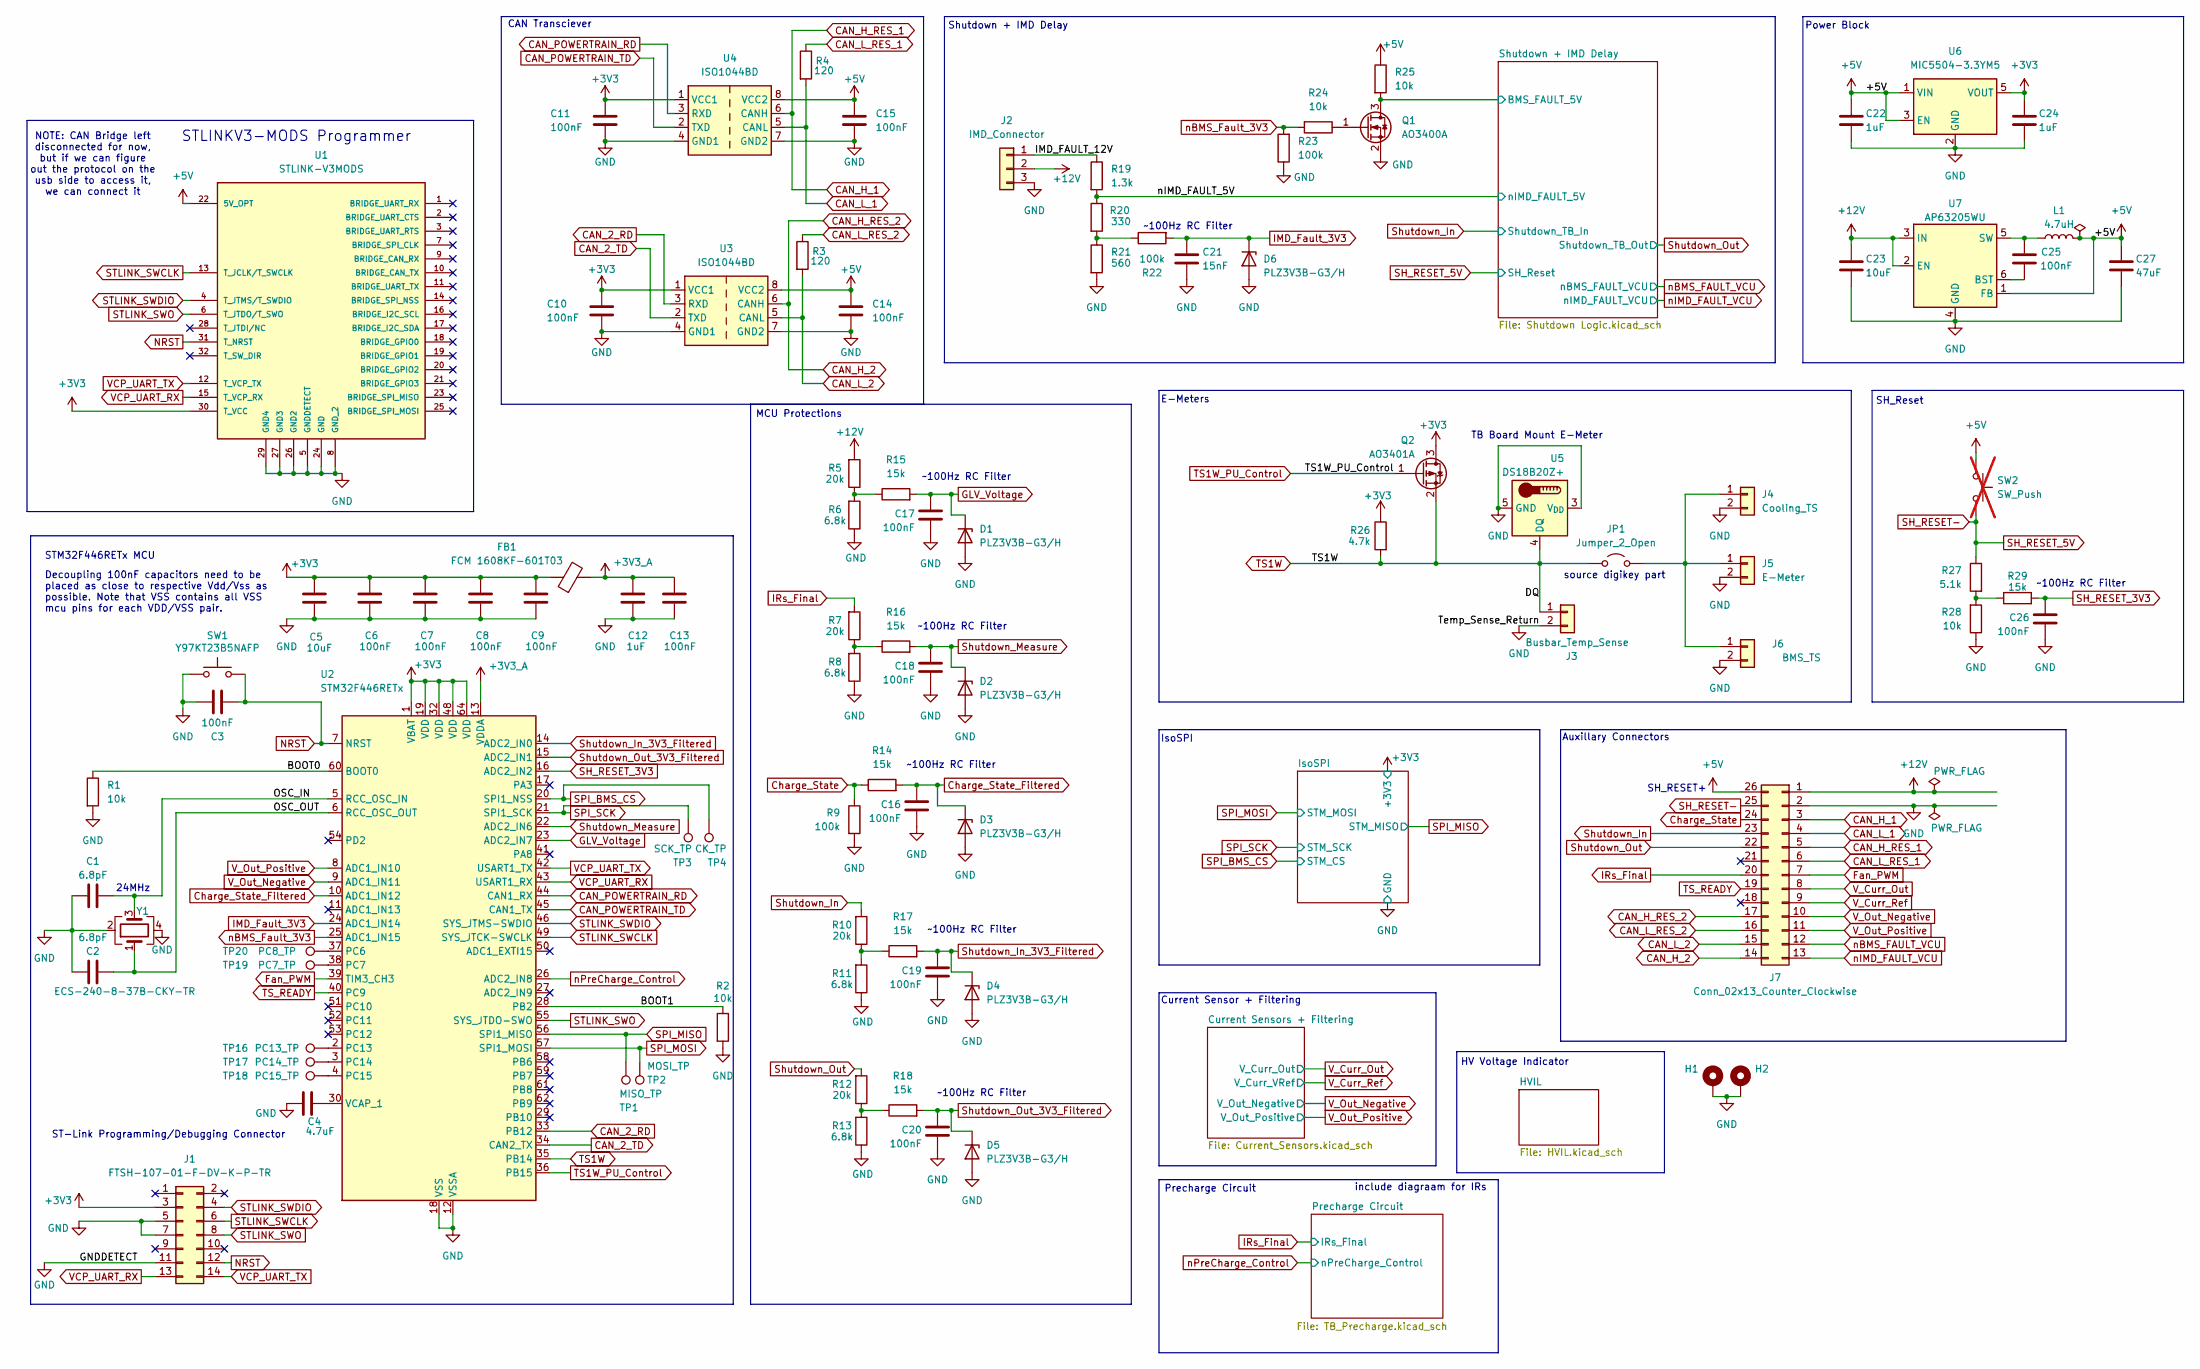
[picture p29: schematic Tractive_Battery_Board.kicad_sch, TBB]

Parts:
C1, C2: 6.8pF; C_0603_1608Metric_Pad1.08x0.95mm_HandSolder; MFG PN CC0603CRNPO9BN6R8; Digi PN 311-3861-1-ND
C3, C6, C7, C8, C9, C10, C11, C13, C14, C15, C16, C17, C18, C19, C20, C25, C26: 100nF; C_0603_1608Metric_Pad1.08x0.95mm_HandSolder; MFG PN CC0603KRX7R8BB104; Digi PN 311-1341-1-ND
C4: 4.7uF; C_0805_2012Metric_Pad1.18x1.45mm_HandSolder; MFG PN CL21A475KAQNNNE; Digi PN 1276-1244-1-ND
C5, C23: 10uF; R_0805_2012Metric_Pad1.20x1.40mm_HandSolder; MFG PN CL21A106KAYNNNE; Digi PN 1276-2891-1-ND
C12, C22, C24: 1uF; C_0603_1608Metric_Pad1.08x0.95mm_HandSolder; MFG PN CC0603KRX7R8BB105; Digi PN 311-1802-1-ND
C21: 15nF; C_0603_1608Metric_Pad1.08x0.95mm_HandSolder; MFG PN CC0603KRX7R8BB153; Digi PN 311-4080-1-ND
C27: 47uF; C_0805_2012Metric_Pad1.18x1.45mm_HandSolder; MFG PN CL21A476MQYNNNE; Digi PN 1276-1852-1-ND
D1, D2, D3, D4, D5, D6: PLZ3V3B-G3/H; D_SMF; MFG PN PLZ3V3B-G3/H; Digi PN PLZ3V3B-G3/HGIDKR-ND
FB1: FCM 1608KF-601T03; L_0603_1608Metric_Pad1.05x0.95mm_HandSolder; MFG PN FCM 1608KF-601T03; Digi PN 4816-FCM1608KF-601T03CT-ND
H1, H2: MountingHole_Pad; MountingHole_3.2mm_M3_Pad
J1: FTSH-107-01-F-DV-K-P-TR; PinHeader_2x07_P1.27mm_Vertical_SMD; MFG PN FTSH-107-01-F-DV-K-P-TR; Digi PN SAM13170CT-ND
J2: IMD_Connector; 1054311103 - 3-Pin Molex Nano-fit; MFG PN 1054311103; Digi PN WM26074CT-ND
J3: Busbar_Temp_Sense; 1054311202 - 2-Pin Molex Nano-fit; MFG PN 1054311102; Digi PN WM26073CT-ND
J4: Cooling_TS; 1054311202 - 2-Pin Molex Nano-fit; MFG PN 1054311102; Digi PN WM26073CT-ND
J5: E-Meter; 1054311202 - 2-Pin Molex Nano-fit; MFG PN 1054311102; Digi PN WM26073CT-ND
J6: BMS_TS; 1054311202 - 2-Pin Molex Nano-fit; MFG PN 1054311102; Digi PN WM26073CT-ND
J7: Conn_02x13_Counter_Clockwise; ATS15-26PA-BM01; MFG PN ATS15-26PA-BM01; Digi PN 889-ATS15-26PA-BM01-ND
JP1: Jumper_2_Open; PinHeader_2x01_P2.54mm_Vertical; MFG PN M20-9990246; Digi PN 952-2262-ND
L1: 4.7uH; L_Bourns_SRP5030T; MFG PN SRP5030T-4R7M; Digi PN SRP5030T-4R7MCT-ND
Q1: AO3400A; SOT-23; MFG PN AO3400A; Digi PN 785-1000-1-ND
Q2: AO3401A; SOT-23; MFG PN AO3401A; Digi PN 785-1001-1-ND
R1, R2, R24, R25, R28: 10k; R_0603_1608Metric_Pad0.98x0.95mm_HandSolder; MFG PN AC0603FR-0710KL; Digi PN 311-10KLDCT-ND
R3, R4: 120; R_0603_1608Metric_Pad0.98x0.95mm_HandSolder; MFG PN RC0603FR-07120RL; Digi PN 311-120HRCT-ND
R5, R7, R10, R12: 20k; R_0603_1608Metric_Pad0.98x0.95mm_HandSolder; MFG PN RC0603FR-0720KL; Digi PN 311-20.0KHRCT-ND
R6, R8, R11, R13: 6.8k; R_0603_1608Metric_Pad0.98x0.95mm_HandSolder; MFG PN AC0603FR-076K8L; Digi PN YAG3627CT-ND
R9, R22, R23: 100k; R_0603_1608Metric_Pad0.98x0.95mm_HandSolder; MFG PN AC0603FR-13100KL; Digi PN 13-AC0603FR-13100KLCT-ND
R14, R15, R16, R17, R18, R29: 15k; R_0603_1608Metric_Pad0.98x0.95mm_HandSolder; MFG PN RC0603FR-0715KL; Digi PN 311-15.0KHRCT-ND
R19: 1.3k; R_2010_5025Metric_Pad1.40x2.65mm_HandSolder; MFG PN AC2010FK-071K3L; Digi PN YAG4005CT-ND
R20: 330; R_1206_3216Metric_Pad1.30x1.75mm_HandSolder; MFG PN RC1206JR-07330RL; Digi PN 311-330ERCT-ND
R21: 560; R_1206_3216Metric_Pad1.30x1.75mm_HandSolder; MFG PN RC1206FR-07560RL; Digi PN 311-560FRCT-ND
R26: 4.7k; R_0603_1608Metric_Pad0.98x0.95mm_HandSolder; MFG PN AC0603FR-074K7L; Digi PN YAG3613CT-ND
R27: 5.1k; R_0603_1608Metric_Pad0.98x0.95mm_HandSolder; MFG PN RC0603FR-075K1L; Digi PN 311-5.10KHRCT-ND
SW1: Y97KT23B5NAFP; SW_SPST_PTS647_Sx38; MFG PN Y97KT23B5NAFP; Digi PN 108-Y97KT23B5NAFPCT-ND
SW2: SW_Push; R_0603_1608Metric_Pad0.98x0.95mm_HandSolder; not fitted
TP1: MISO_TP; TestPoint_Pad_D1.0mm
TP2: MOSI_TP; TestPoint_Pad_D1.0mm
TP3: SCK_TP; TestPoint_Pad_D1.0mm
TP4: CK_TP; TestPoint_Pad_D1.0mm
TP16: PC13_TP; TestPoint_Pad_D1.0mm
TP17: PC14_TP; TestPoint_Pad_D1.0mm
TP18: PC15_TP; TestPoint_Pad_D1.0mm
TP19: PC7_TP; TestPoint_Pad_D1.0mm
TP20: PC8_TP; TestPoint_Pad_D1.0mm
U1: STLINK-V3MODS; MODULE_STLINK-V3MODS; PARTREV 1; Digi PN 497-STLINK-V3MODS-ND
U2: STM32F446RETx; LQFP-64_10x10mm_P0.5mm; MFG PN STM32F446RET6; Digi PN 497-15376-ND
U3, U4: ISO1044BD; SOIC-8_ISO1044BD; MFG PN ISO1044BD; Digi PN 296-ISO1044BD-ND
U5: DS18B20Z+; SOIC-8_3.9x4.9mm_P1.27mm; MFG PN DS18B20Z+; Digi PN DS18B20Z+-ND
U6: MIC5504-3.3YM5; SOT-23-5; MFG PN MIC5504-3.3YM5-TR; Digi PN 576-4764-1-ND
U7: AP63205WU; TSOT-23-6; MFG PN AP63205WU-7; Digi PN AP63205WU-7DICT-ND
Y1: ECS-240-8-37B-CKY-TR; Crystal_SMD_2016-4Pin_2.0x1.6mm; MFG PN ECS-240-8-37B-CKY-TR; Digi PN XC3063CT-ND

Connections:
+3V3: C5.2, C6.1, C7.1, C8.1, C9.1, C10.1, C11.1, C24.2, FB1.1, J1.3, Q2.3 (D), R26.1, U1.30 (T_VCC), U2.1 (VBAT), U2.19 (VDD), U2.32 (VDD), U2.48 (VDD), U2.64 (VDD), U3.1 (VCC1), U4.1 (VCC1), U6.5 (VOUT); also elsewhere on the board
+3V3_A: C12.1, C13.1, FB1.2, U2.13 (VDDA)
+5V: C14.1, C15.1, C22.2, C27.2, J7.26, L1.2, R25.1, U1.22 (5V_OPT), U3.8 (VCC2), U4.8 (VCC2), U6.1 (VIN), U6.3 (EN), U7.1 (FB); also elsewhere on the board
+12V: C23.2, J2.2, J7.1, R5.2, U7.2 (EN), U7.3 (IN); also elsewhere on the board
/BOOT0: R1.1, U2.60 (BOOT0)
/BOOT1: R2.1, U2.28 (PB2)
/IMD_FAULT_12V: J2.1, R19.1
/OSC_IN: C1.1, U2.5 (RCC_OSC_IN), Y1.3
/OSC_OUT: C2.1, U2.6 (RCC_OSC_OUT), Y1.1
/Shutdown + IMD Delay/BMS_FAULT_5V: Q1.3 (D), R25.2; also elsewhere on the board
/nIMD_FAULT_5V: R19.2, R20.1; also elsewhere on the board
CAN_2_RD: U2.33 (PB12), U3.3 (RXD)
CAN_2_TD: U2.34 (CAN2_TX), U3.2 (TXD)
CAN_H_1: J7.3, J7.5, U4.6 (CANH)
CAN_H_2: J7.14, J7.17, U3.6 (CANH)
CAN_L_1: J7.4, R4.2, U4.5 (CANL)
CAN_L_2: J7.15, R3.2, U3.5 (CANL)
CAN_L_RES_1: J7.6, R4.1
CAN_L_RES_2: J7.16, R3.1
CAN_POWERTRAIN_RD: U2.44 (CAN1_RX), U4.3 (RXD)
CAN_POWERTRAIN_TD: U2.45 (CAN1_TX), U4.2 (TXD)
Charge_State: J7.24, R9.1, R14.1
Charge_State_Filtered: C16.1, D3.1 (K), R14.2, U2.10 (ADC1_IN12)
Fan_PWM: J7.7, U2.39 (TIM3_CH3)
GLV_Voltage: C17.1, D1.1 (K), R15.2, U2.23 (ADC2_IN7)
GND: C1.2, C2.2, C3.1, C4.1, C5.1, C6.2, C7.2, C8.2, C9.2, C10.2, C11.2, C12.2, C13.2, C14.2, C15.2, C16.2, C17.2, C18.2, C19.2, C20.2, C21.2, C22.1, C23.1, C24.1, C26.2, C27.1, D1.2 (A), D2.2 (A), D3.2 (A), D4.2 (A), D5.2 (A), D6.2 (A), H1.1, H2.1, J1.5, J1.7, J1.11, J2.3, J3.2, J4.2, J5.2, J6.2, J7.2, Q1.2 (S), R1.2, R2.2, R6.1, R8.1, R9.2, R11.1, R13.1, R21.2, R23.1, R28.1, SW1.1, U1.5 (GNDDETECT), U1.8 (GND_2), U1.24 (GND), U1.26 (GND2), U1.27 (GND3), U1.29 (GND4), U2.12 (VSSA), U2.18 (VSS), U2.31 (VSS), U2.47 (VSS), U2.63 (VSS), U3.4 (GND1), U3.7 (GND2), U4.4 (GND1), U4.7 (GND2), U5.3 (V_{DD}), U5.5 (GND), U6.2 (GND), U7.4 (GND), Y1.2, Y1.4; also elsewhere on the board
IMD_Fault_3V3: C21.1, D6.1 (K), R22.2, U2.24 (ADC1_IN14)
IRs_Final: J7.20, R7.2; also elsewhere on the board
NRST: C3.2, J1.12, SW1.2, U1.31 (T_NRST), U2.7 (NRST)
unnamed: J4.1, J5.1, J6.1, JP1.1 (A)
unnamed: Q1.1 (G), R24.1
unnamed: R10.1, R11.2, R17.1
unnamed: R12.1, R13.2, R18.1
unnamed: R5.1, R6.2, R15.1
unnamed: R7.1, R8.2, R16.1
unnamed: R20.2, R21.1, R22.1
unnamed: R27.2, R28.2, R29.1
unnamed: TP20.1, U2.37 (PC6)
unnamed: TP19.1, U2.38 (PC7)
unnamed: TP16.1, U2.2 (PC13)
unnamed: TP17.1, U2.3 (PC14)
unnamed: TP18.1, U2.4 (PC15)
unnamed: C4.2, U2.30 (VCAP_1)
unnamed: C25.2, U7.6 (BST)
unnamed: C25.1, L1.1, U7.5 (SW)
SH_RESET-: J7.25, R27.1, SW2.2; also elsewhere on the board
SH_RESET_3V3: C26.1, R29.2, U2.16 (ADC2_IN2)
SPI_BMS_CS: TP4.1, U2.20 (SPI1_NSS); also elsewhere on the board
SPI_MISO: TP1.1, U2.56 (SPI1_MISO); also elsewhere on the board
SPI_MOSI: TP2.1, U2.57 (SPI1_MOSI); also elsewhere on the board
SPI_SCK: TP3.1, U2.21 (SPI1_SCK); also elsewhere on the board
STLINK_SWCLK: J1.6, U1.13 (T_JCLK/T_SWCLK), U2.49 (SYS_JTCK-SWCLK)
STLINK_SWDIO: J1.4, U1.4 (T_JTMS/T_SWDIO), U2.46 (SYS_JTMS-SWDIO)
STLINK_SWO: J1.8, U1.6 (T_JTDO/T_SWO), U2.55 (SYS_JTDO-SWO)
Shutdown_In: J7.23, R10.2; also elsewhere on the board
Shutdown_In_3V3_Filtered: C19.1, D4.1 (K), R17.2, U2.14 (ADC2_IN0)
Shutdown_Measure: C18.1, D2.1 (K), R16.2, U2.22 (ADC2_IN6)
Shutdown_Out: J7.22, R12.2; also elsewhere on the board
Shutdown_Out_3V3_Filtered: C20.1, D5.1 (K), R18.2, U2.15 (ADC2_IN1)
TS1W: J3.1, JP1.2 (B), Q2.2 (S), R26.2, U2.35 (PB14), U5.4 (DQ)
TS1W_PU_Control: Q2.1 (G), U2.36 (PB15)
TS_READY: J7.19, U2.40 (PC9)
VCP_UART_RX: J1.13, U1.15 (T_VCP_RX), U2.43 (USART1_RX)
VCP_UART_TX: J1.14, U1.12 (T_VCP_TX), U2.42 (USART1_TX)
V_Curr_Out: J7.8; also elsewhere on the board
V_Curr_Ref: J7.9; also elsewhere on the board
V_Out_Negative: J7.10, U2.9 (ADC1_IN11); also elsewhere on the board
V_Out_Positive: J7.11, U2.8 (ADC1_IN10); also elsewhere on the board
nBMS_FAULT_VCU: J7.12; also elsewhere on the board
nBMS_Fault_3V3: R23.2, R24.2, U2.25 (ADC1_IN15)
nIMD_FAULT_VCU: J7.13; also elsewhere on the board
nPreCharge_Control: U2.26 (ADC2_IN8); also elsewhere on the board

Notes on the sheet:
~100Hz RC Filter
SH_Reset
Power Block
ST-Link Programming/Debugging Connector
Decoupling 100nF capacitors need to be placed as close to respective Vdd/Vss as possible. Note that VSS contains all VSS mcu pins for each VDD/VSS pair.
STLINKV3-MODS Programmer
MCU Protections
STM32F446RETx MCU
NOTE: CAN Bridge left disconnected for now, but if we can figure out the protocol on the usb side to access it, we can connect it
HV Voltage Indicator
CAN Transciever
E-Meters
24MHz
Precharge Circuit
IsoSPI
SH_RESET+
TB Board Mount E-Meter
include diagraam for IRs
Current Sensor + Filtering
source digikey part
Shutdown + IMD Delay
Auxillary Connectors

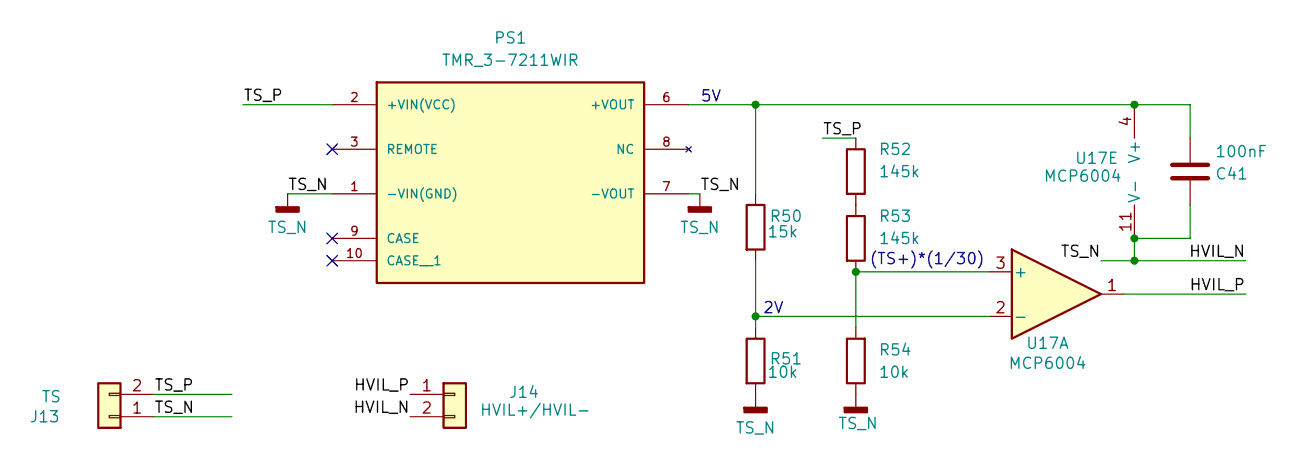
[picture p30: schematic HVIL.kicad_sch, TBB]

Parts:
C41: 100nF; C_0603_1608Metric_Pad1.08x0.95mm_HandSolder; MFG PN CC0603KRX7R8BB104; Digi PN 311-1341-1-ND
J13: TS; 1054311202 - 2-Pin Molex Nano-fit; MFG PN 1054311102; Digi PN WM26073CT-ND
J14: HVIL+/HVIL-; 1054311202 - 2-Pin Molex Nano-fit; MFG PN 1054311102; Digi PN WM26073CT-ND
PS1: TMR_3-7211WIR; TMR 3-7211WIR; MFG PN TMR 3-7211WIR; Digi PN 1951-2005-ND
R50: 15k; R_0603_1608Metric_Pad0.98x0.95mm_HandSolder; MFG PN RC0603FR-0715KL; Digi PN 311-15.0KHRCT-ND
R51, R54: 10k; R_0603_1608Metric_Pad0.98x0.95mm_HandSolder; MFG PN AC0603FR-0710KL; Digi PN 311-10KLDCT-ND
R52, R53: 145k; R_0805_2012Metric_Pad1.20x1.40mm_HandSolder; MFG PN RT0805BRD07145KL; Digi PN 13-RT0805BRD07145KLCT-ND
U17: MCP6004; SOIC-14_3.9x8.7mm_P1.27mm; MFG PN MCP6004T-I/SL; Digi PN MCP6004T-I/SLCT-ND

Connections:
/HVIL/HVIL_P: J14.1, U17.1
/HVIL/TS_P: J13.2, PS1.2 (+VIN(VCC)), R52.1
unnamed: C41.2, PS1.6 (+VOUT), R50.1, U17.4 (V+)
unnamed: R52.2, R53.1
unnamed: R53.2, R54.2, U17.3 (+)
unnamed: R50.2, R51.1, U17.2 (-)
TS_N: C41.1, J13.1, J14.2, PS1.1 (-VIN(GND)), PS1.7 (-VOUT), R51.2, R54.1, U17.11 (V-)

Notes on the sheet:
(TS+)*(1/30)

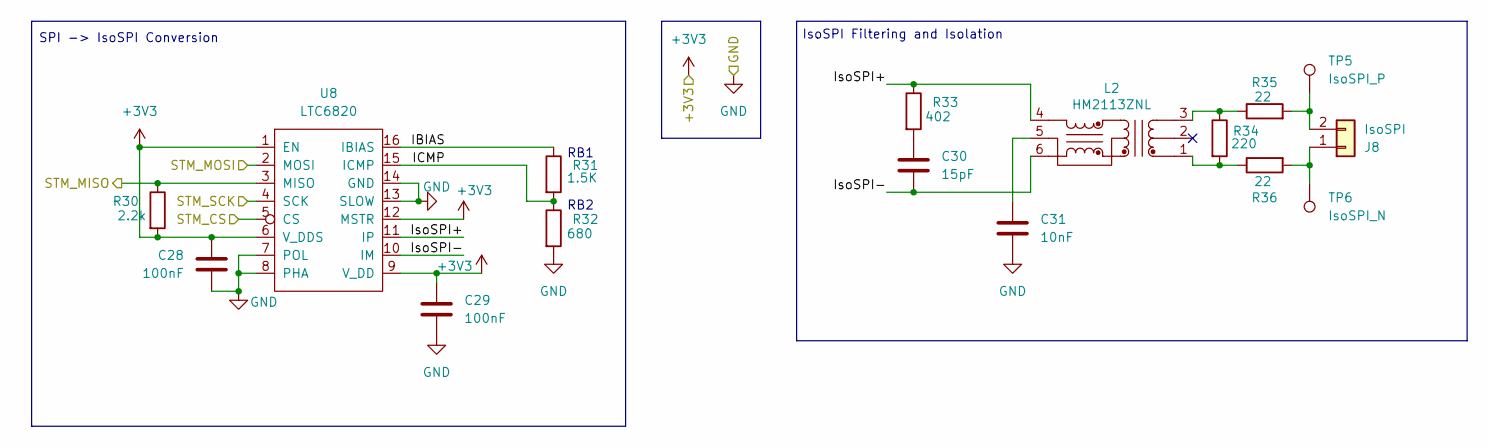
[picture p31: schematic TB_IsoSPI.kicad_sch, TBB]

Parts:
C28, C29: 100nF; C_0603_1608Metric_Pad1.08x0.95mm_HandSolder; MFG PN CC0603KRX7R8BB104; Digi PN 311-1341-1-ND
C30: 15pF; C_0603_1608Metric_Pad1.08x0.95mm_HandSolder; MFG PN CC0603JRNPO9BN150; Digi PN 311-1060-1-ND
C31: 10nF; C_0603_1608Metric_Pad1.08x0.95mm_HandSolder; MFG PN CC0603KPX7R8BB103; Digi PN 13-CC0603KPX7R8BB103CT-ND
J8: IsoSPI; 1054311202 - 2-Pin Molex Nano-fit; MFG PN 1054311102; Digi PN WM26073CT-ND
L2: HM2113ZNL; HM2113ZNLT; MFG PN HM2113ZNLT; Digi PN 553-HM2113ZNLTCT-ND
R30: 2.2k; R_0603_1608Metric_Pad0.98x0.95mm_HandSolder; MFG PN RC0603FR-072K2L; Digi PN 311-2.20KHRCT-ND
R31: 1.5K; R_0603_1608Metric_Pad0.98x0.95mm_HandSolder; MFG PN RC0603FR-071K5L; Digi PN 311-1.50KHRCT-ND
R32: 680; R_0603_1608Metric_Pad0.98x0.95mm_HandSolder; MFG PN RC0603FR-07680RL; Digi PN 311-680HRCT-ND
R33: 402; R_0603_1608Metric_Pad0.98x0.95mm_HandSolder; MFG PN AC0603FR-07402RL; Digi PN 13-AC0603FR-07402RLCT-ND
R34: 220; R_0603_1608Metric_Pad0.98x0.95mm_HandSolder; MFG PN RC0603FR-07220RL; Digi PN 311-220HRCT-ND
R35, R36: 22; R_0603_1608Metric_Pad0.98x0.95mm_HandSolder; MFG PN RC0603FR-0722RL; Digi PN 311-22.0HRCT-ND
TP5: IsoSPI_P; TestPoint_Pad_D1.0mm
TP6: IsoSPI_N; TestPoint_Pad_D1.0mm
U8: LTC6820; MSOP-16_3x4.039mm_P0.5mm; MFG PN LTC6820HMS#3ZZTRPBF; Digi PN 505-LTC6820HMS#3ZZTRPBFCT-ND

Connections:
+3V3: C28.1, C29.1, R30.2, U8.1 (EN), U8.6 (V_DDS), U8.9 (V_DD), U8.12 (MSTR); also elsewhere on the board
/IsoSPI/IBIAS: R31.1, U8.16 (IBIAS)
/IsoSPI/ICMP: R31.2, R32.1, U8.15 (ICMP)
/IsoSPI/IsoSPI+: L2.4, R33.1, U8.11 (IP)
/IsoSPI/IsoSPI-: C30.2, L2.6, U8.10 (IM)
GND: C28.2, C29.2, C31.2, R32.2, U8.7 (POL), U8.8 (PHA), U8.13 (SLOW), U8.14 (GND); also elsewhere on the board
unnamed: C30.1, R33.2
unnamed: C31.1, L2.5
unnamed: J8.1, R36.2, TP6.1
unnamed: J8.2, R35.2, TP5.1
unnamed: L2.1, R34.2, R36.1
unnamed: L2.3, R34.1, R35.1
SPI_BMS_CS: U8.5 (CS); also elsewhere on the board
SPI_MISO: R30.1, U8.3 (MISO); also elsewhere on the board
SPI_MOSI: U8.2 (MOSI); also elsewhere on the board
SPI_SCK: U8.4 (SCK); also elsewhere on the board

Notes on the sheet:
IsoSPI Filtering and Isolation
RB2
SPI -> IsoSPI Conversion
RB1

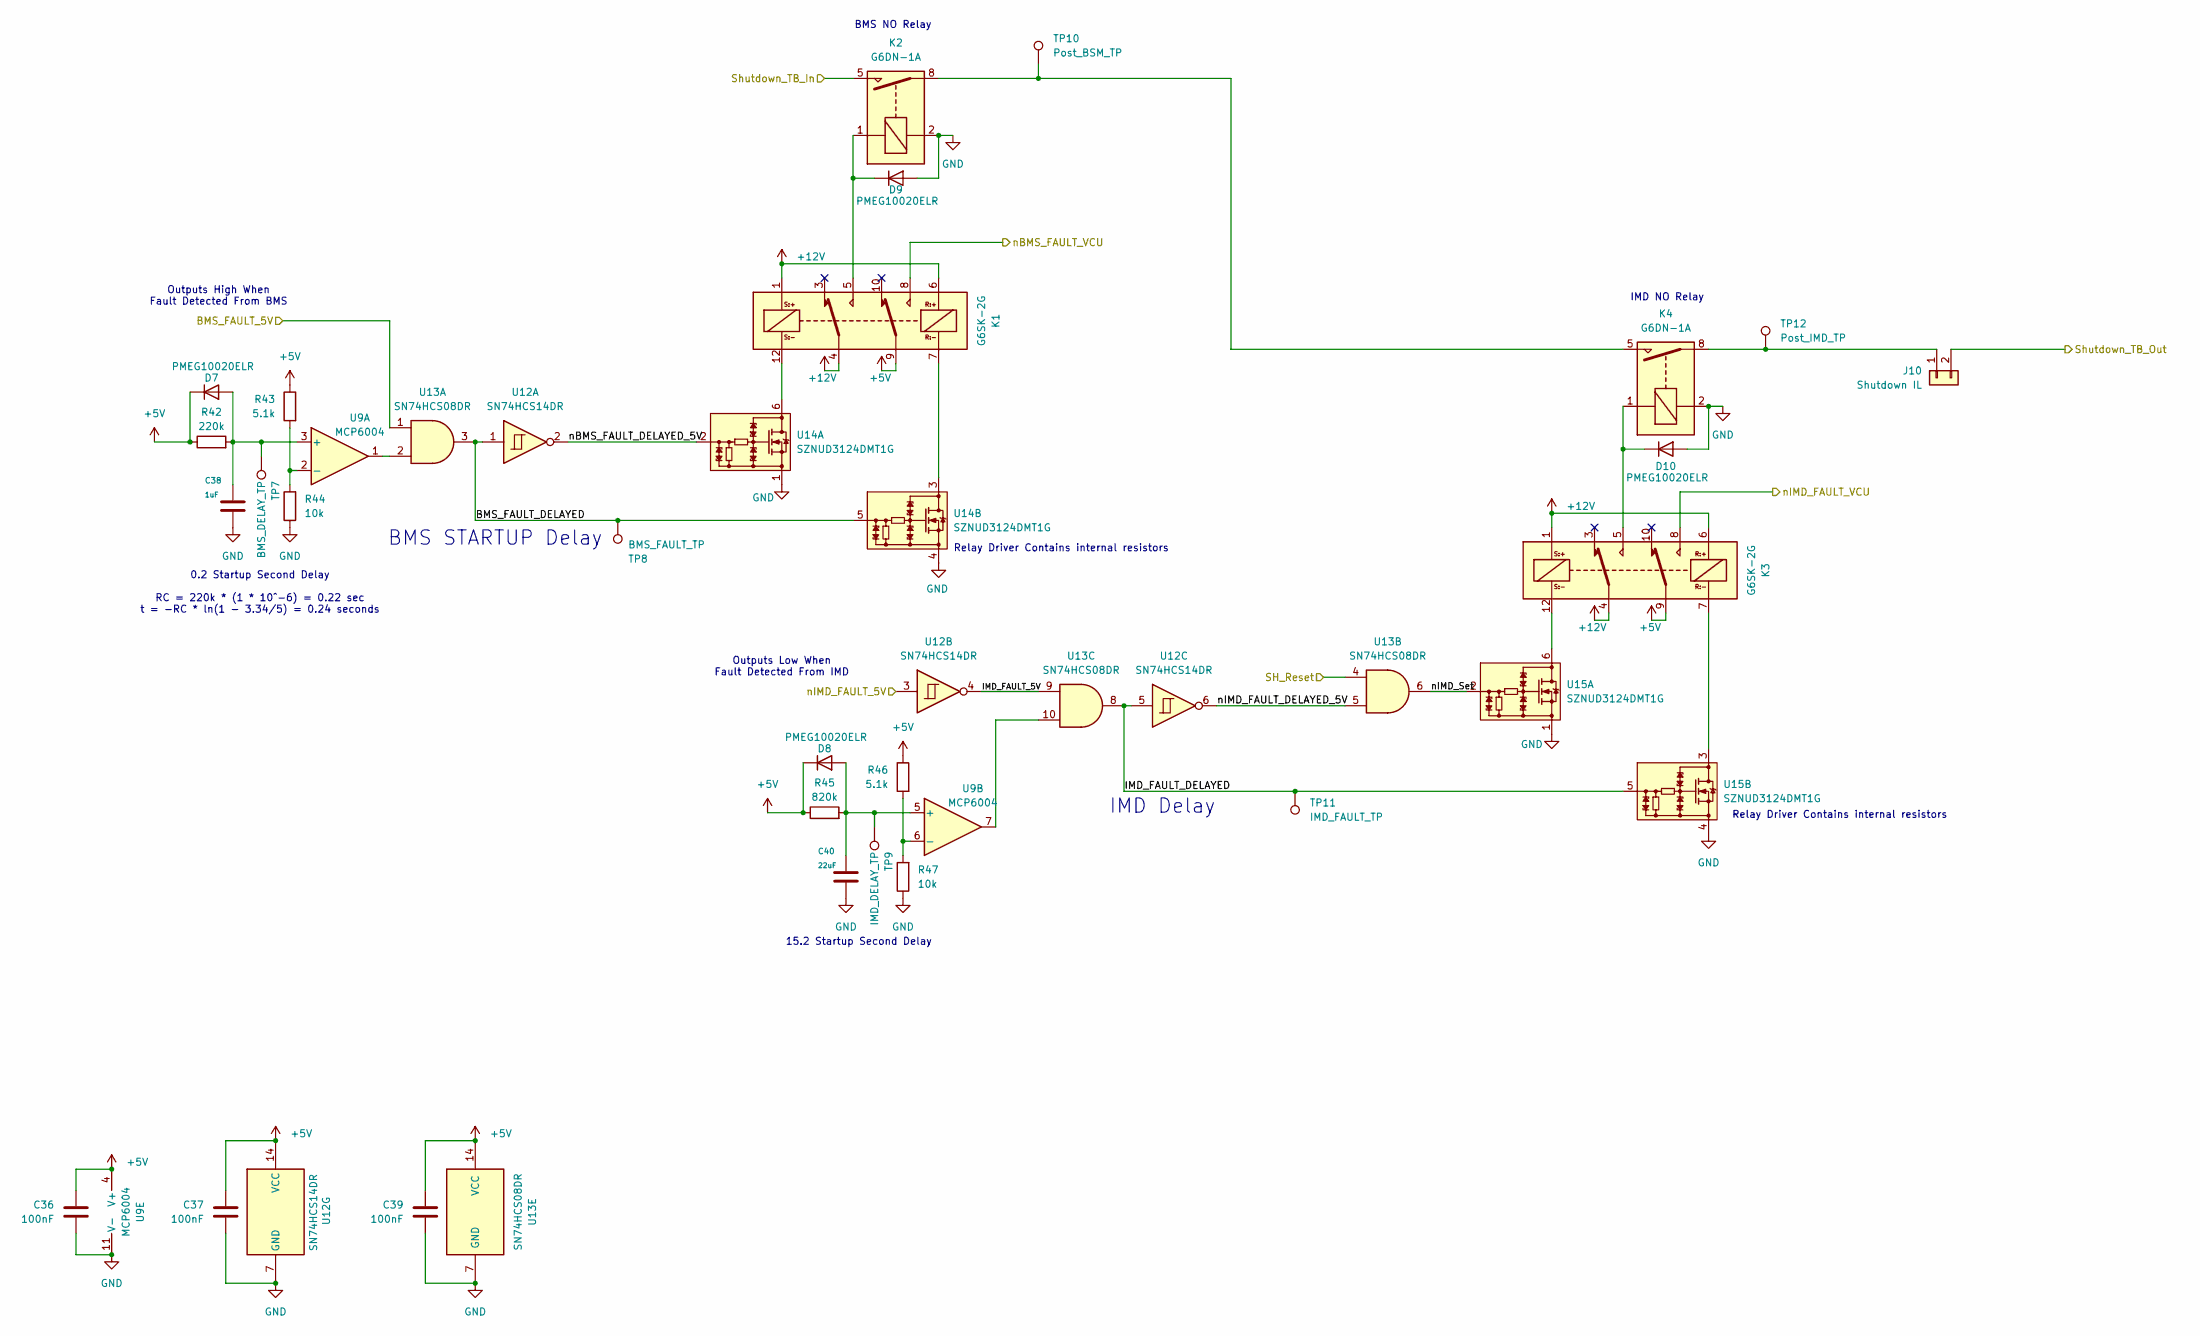
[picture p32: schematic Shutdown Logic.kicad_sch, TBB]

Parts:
C36, C37, C39: 100nF; C_0603_1608Metric_Pad1.08x0.95mm_HandSolder; MFG PN CC0603KRX7R8BB104; Digi PN 311-1341-1-ND
C38: 1uF; C_0603_1608Metric_Pad1.08x0.95mm_HandSolder; MFG PN CC0603KRX7R8BB105; Digi PN 311-1802-1-ND
C40: 22uF; C_0603_1608Metric_Pad1.08x0.95mm_HandSolder; MFG PN CL10A226MP8NUNE; Digi PN 1276-1274-1-ND
D7, D8, D9, D10: PMEG10020ELR; Nexperia_CFP3_SOD-123W; MFG PN PMEG10020ELR-QX; Digi PN 1727-PMEG10020ELR-QXCT-ND
J10: Shutdown IL; 1054311202 - 2-Pin Molex Nano-fit; MFG PN 1054311102; Digi PN WM26073CT-ND
K1, K3: G6SK-2G; Relay_DPDT_Omron_G6SK-2G; MFG PN G6SK-2G DC24; Digi PN Z12726-ND
K2, K4: G6DN-1A; RELAY_G6DN-1A; MFG PN G6DN-1A DC12; Digi PN Z5440-ND
R42: 220k; R_0603_1608Metric_Pad0.98x0.95mm_HandSolder; MFG PN AC0603FR-07220KL; Digi PN YAG3579CT-ND
R43, R46: 5.1k; R_0603_1608Metric_Pad0.98x0.95mm_HandSolder; MFG PN RC0603FR-075K1L; Digi PN 311-5.10KHRCT-ND
R44, R47: 10k; R_0603_1608Metric_Pad0.98x0.95mm_HandSolder; MFG PN AC0603FR-0710KL; Digi PN 311-10KLDCT-ND
R45: 820k; R_0603_1608Metric_Pad0.98x0.95mm_HandSolder; MFG PN RC0603JR-07820KL; Digi PN 311-820KGRCT-ND
TP7: BMS_DELAY_TP; TestPoint_Pad_D1.0mm
TP8: BMS_FAULT_TP; TestPoint_Pad_D1.0mm
TP9: IMD_DELAY_TP; TestPoint_Pad_D1.0mm
TP10: Post_BSM_TP; TestPoint_Pad_D1.0mm
TP11: IMD_FAULT_TP; TestPoint_Pad_D1.0mm
TP12: Post_IMD_TP; TestPoint_Pad_D1.0mm
U9: MCP6004; SOIC-14_3.9x8.7mm_P1.27mm; MFG PN MCP6004T-I/SL; Digi PN MCP6004T-I/SLCT-ND
U12: SN74HCS14DR; SOIC-14_3.9x8.7mm_P1.27mm; MFG PN SN74HCS14DR; Digi PN 296-SN74HCS14DRDKR-ND
U13: SN74HCS08DR; SOIC-14_3.9x8.7mm_P1.27mm; MFG PN SN74HCS08DR; Digi PN 296-SN74HCS08DRCT-ND
U14, U15: SZNUD3124DMT1G; SC-74-6_1.55x2.9mm_P0.95mm; MFG PN SZNUD3124DMT1G; Digi PN SZNUD3124DMT1GOSCT-ND

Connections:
+5V: C36.1, C37.1, C39.1, D7.1 (K), D8.1 (K), K1.9, K3.9, R42.1, R43.1, R45.1, R46.1, U9.4 (V+), U12.14 (VCC), U13.14 (VCC); also elsewhere on the board
+12V: K1.1, K1.4, K1.6, K3.1, K3.4, K3.6; also elsewhere on the board
/Shutdown + IMD Delay/BMS_FAULT_5V: U13.1; also elsewhere on the board
/Shutdown + IMD Delay/BMS_FAULT_DELAYED: TP8.1, U12.1, U13.3, U14.5
/Shutdown + IMD Delay/IMD_FAULT_5V: U12.4, U13.9
/Shutdown + IMD Delay/IMD_FAULT_DELAYED: TP11.1, U12.5, U13.8, U15.5
/Shutdown + IMD Delay/nBMS_FAULT_DELAYED_5V: U12.2, U14.2
/Shutdown + IMD Delay/nIMD_FAULT_DELAYED_5V: U12.6, U13.5
/Shutdown + IMD Delay/nIMD_Set: U13.6, U15.2
/nIMD_FAULT_5V: U12.3; also elsewhere on the board
GND: C36.2, C37.2, C38.2, C39.2, C40.2, D9.2 (A), D10.2 (A), K2.2, K4.2, R44.1, R47.1, U9.11 (V-), U12.7 (GND), U13.7 (GND), U14.1, U14.4, U15.1, U15.4; also elsewhere on the board
unnamed: C38.1, D7.2 (A), R42.2, TP7.1, U9.3 (+)
unnamed: C40.1, D8.2 (A), R45.2, TP9.1, U9.5 (+)
unnamed: D9.1 (K), K1.5, K2.1
unnamed: D10.1 (K), K3.5, K4.1
unnamed: J10.1, K4.8, TP12.1
unnamed: K1.7, U14.3
unnamed: K1.12, U14.6
unnamed: K2.8, K4.5, TP10.1
unnamed: K3.7, U15.3
unnamed: K3.12, U15.6
unnamed: R43.2, R44.2, U9.2 (-)
unnamed: R46.2, R47.2, U9.6 (-)
unnamed: U9.1, U13.2
unnamed: U9.7, U13.10
SH_RESET-: U13.4; also elsewhere on the board
Shutdown_In: K2.5; also elsewhere on the board
Shutdown_Out: J10.2; also elsewhere on the board
nBMS_FAULT_VCU: K1.8; also elsewhere on the board
nIMD_FAULT_VCU: K3.8; also elsewhere on the board

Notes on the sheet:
Relay Driver Contains internal resistors
IMD Delay
0.2 Startup Second Delay RC = 220k * (1 * 10^-6) = 0.22 sec t = -RC * ln(1 - 3.34/5) = 0.24 seconds
15.2 Startup Second Delay
BMS NO Relay
Outputs High When Fault Detected From BMS
Outputs Low When Fault Detected From IMD
IMD NO Relay
BMS STARTUP Delay


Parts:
C32, C33: 22nF; C_0603_1608Metric_Pad1.08x0.95mm_HandSolder; MFG PN CC0603KRX7R8BB223; Digi PN 311-1086-1-ND
C34, C35, C42: 100nF; C_0603_1608Metric_Pad1.08x0.95mm_HandSolder; MFG PN CC0603KRX7R8BB104; Digi PN 311-1341-1-ND
D11, D12: PLZ3V3B-G3/H; D_SMF; MFG PN PLZ3V3B-G3/H; Digi PN PLZ3V3B-G3/HGIDKR-ND
J9: Current Sensor; 1054311104 - 4-pin Molex Nano-fit; MFG PN 1054311104; Digi PN WM26075CT-ND
R37: 10k; R_0603_1608Metric_Pad0.98x0.95mm_HandSolder; MFG PN AC0603FR-0710KL; Digi PN 311-10KLDCT-ND
R38, R39: 22.1k; R_0603_1608Metric_Pad0.98x0.95mm_HandSolder; MFG PN RC0603FR-0722K1L; Digi PN 311-22.1KHRCT-ND
R40, R41: 62k; R_0603_1608Metric_Pad0.98x0.95mm_HandSolder; MFG PN RMCF0603FT62K0; Digi PN RMCF0603FT62K0CT-ND
R55, R56: 15k; R_0603_1608Metric_Pad0.98x0.95mm_HandSolder; MFG PN RC0603FR-0715KL; Digi PN 311-15.0KHRCT-ND
R57: 10k; R_0603_1608Metric_Pad0.98x0.95mm_HandSolder; MFG PN RC0603FR-0710KL; Digi PN 311-10.0KHRCT-ND
R58: 237k; R_0603_1608Metric_Pad0.98x0.95mm_HandSolder; MFG PN RC0603FR-07237KL; Digi PN 311-237KHRCT-ND
U9, U18: MCP6004; SOIC-14_3.9x8.7mm_P1.27mm; MFG PN MCP6004T-I/SL; Digi PN MCP6004T-I/SLCT-ND
U10, U11: INA826AIDR; SOIC-8_3.9x4.9mm_P1.27mm; MFG PN INA826AIDR; Digi PN 296-30238-1-ND

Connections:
+5V: C34.1, C35.1, C42.1, J9.4, R57.1, U10.8 (V+), U11.8 (V+), U18.4 (V+); also elsewhere on the board
/Current Sensors + Filtering/Raw_Curr_Out: J9.2, R37.1, R38.2
/Current Sensors + Filtering/Raw_Curr_VRef: J9.1, R39.2
GND: C32.2, C33.2, C34.2, C35.2, C42.2, D11.2 (A), D12.2 (A), J9.3, R37.2, R58.2, U10.5 (V-), U11.5 (V-), U18.11 (V-); also elsewhere on the board
unnamed: R40.1, U10.2 (Rg)
unnamed: R40.2, U10.3 (Rg)
unnamed: R41.1, U11.2 (Rg)
unnamed: R41.2, U11.3 (Rg)
unnamed: R55.1, U11.7
unnamed: R56.1, U10.7
unnamed: C32.1, R38.1, U9.10 (+)
unnamed: C33.1, R39.1, U9.12 (+)
unnamed: U10.6 (Ref), U11.6 (Ref), U18.1, U18.2 (-)
unnamed: R57.2, R58.1, U18.3 (+)
V_Curr_Out: U9.8, U9.9 (-), U10.1 (-), U11.4 (+); also elsewhere on the board
V_Curr_Ref: U9.13 (-), U9.14, U10.4 (+), U11.1 (-); also elsewhere on the board
V_Out_Negative: D11.1 (K), R55.2; also elsewhere on the board
V_Out_Positive: D12.1 (K), R56.2; also elsewhere on the board

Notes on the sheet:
RC Filter --> 1/(2 * pi * 22,100* 22 * 10^(-9)) = ~327.3Hz
Document and ideal gain. note down theoretical resistor error +- 1% Resistors for the 62k resistor
GAIN = 1.78 GAIN = 1 + 49.4k/R_G R_G = ~63.333k ohms
0.2 VREF
10x R, C/10
V_out = 0 < V < 3V3 A = gain = V_out/(V_ref-V_curr_out) = 3.3 / 1.875 = 1.76 (minimum current) V_curr_out = 2.5V + (0.625 * 900A/300A) = 4.375V OR 2.5V + (0.625 * -900A/300A) = 0.625V V_ref = 2.5V + (0.625 * 0A/300A) = 2.5V


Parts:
J11: IRs Power; 1054311104 - 4-pin Molex Nano-fit; MFG PN 1054311104; Digi PN WM26075CT-ND
J12: Precharge; 1054311202 - 2-Pin Molex Nano-fit; MFG PN 1054311102; Digi PN WM26073CT-ND
K5: PR30-12V-450-1A-E; RELAY_PR30-12V-450-1A-E; MFG PN PR30-12V-450-1A-E; Digi PN 2223-PR30-12V-450-1A-E-ND
Q3: AO3400A; SOT-23; MFG PN AO3400A; Digi PN 785-1000-1-ND
R48: 100k; R_0603_1608Metric_Pad0.98x0.95mm_HandSolder; MFG PN AC0603FR-13100KL; Digi PN 13-AC0603FR-13100KLCT-ND
R49: 10k; R_0603_1608Metric_Pad0.98x0.95mm_HandSolder; MFG PN AC0603FR-0710KL; Digi PN 311-10KLDCT-ND
U12: SN74HCS14DR; SOIC-14_3.9x8.7mm_P1.27mm; MFG PN SN74HCS14DR; Digi PN 296-SN74HCS14DRDKR-ND
U16: SZNUD3124LT1G; TSOT-23_HandSoldering; MFG PN SZNUD3124LT1G; Digi PN SZNUD3124LT1GOSCT-ND

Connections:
GND: J11.3, Q3.2 (S), R48.2, U16.2; also elsewhere on the board
IRs_Final: J11.2, J11.4, K5.A2; also elsewhere on the board
unnamed: J11.1, Q3.3 (D)
unnamed: J12.1, K5.5
unnamed: J12.2, K5.8
unnamed: K5.A1, U16.3
unnamed: Q3.1 (G), R49.2
unnamed: U12.8, U16.1
nPreCharge_Control: R48.1, R49.1, U12.9; also elsewhere on the board

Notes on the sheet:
nPrecharge_Control outputs LOW during precharge

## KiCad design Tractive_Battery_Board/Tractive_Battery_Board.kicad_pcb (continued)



Board: 4 copper layers, 139.7 x 63.5 mm, 178 parts (10 on the bottom side), 127 nets.

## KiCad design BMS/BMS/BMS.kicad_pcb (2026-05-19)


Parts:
C1, C8: 10nF; C_0805_2012Metric_Pad1.18x1.45mm_HandSolder; MFG PN AC0805KRX7R9BB103; Digi PN 311-3174-1-ND
C2, C6: 100nF; C_0805_2012Metric_Pad1.18x1.45mm_HandSolder; MFG PN CC0805KKX7R0BB104; Digi PN 311-2083-1-ND
C3, C4, C5: 1uF; C_0805_2012Metric_Pad1.18x1.45mm_HandSolder; MFG PN CC0805KFX7R9BB105; Digi PN 13-CC0805KFX7R9BB105CT-ND
C7: 15pF; C_0805_2012Metric_Pad1.18x1.45mm_HandSolder; MFG PN CC0805KRNPO9BN150; Digi PN 13-CC0805KRNPO9BN150CT-ND
D1, D2: LH R974-LP-1; LED_0805_2012Metric_Pad1.15x1.40mm_HandSolder; MFG PN LS R976-NR-1-0-20-R18; Digi PN 475-LSR976-NR-1CT-ND
J1, J2: 84952-5; 849525; MFG PN 84952-5; Digi PN A101386CT-ND
J3, J5: 512810598; MFG PN 0512810598; Digi PN 900-0512810598CT-ND
J4, J6, J7, J8: 1053131202; Nano-Fit_1054301102; MFG PN 1054301202; Digi PN WM26097CT-ND
L1: HM2113ZNLT; MFG PN HM2113ZNLT; Digi PN 553-HM2113ZNLTCT-ND
Q1: NSV1C201MZ4; SOT-223; MFG PN NSS1C201MZ4T1G; Digi PN NSS1C201MZ4T1GOSCT-ND
R1, R4: 100; R_0805_2012Metric_Pad1.20x1.40mm_HandSolder; MFG PN RC0805FR-07100RL; Digi PN 311-100CRCT-ND
R2: 10; R_0805_2012Metric_Pad1.20x1.40mm_HandSolder; MFG PN RC0805FR-1010RL; Digi PN 13-RC0805FR-1010RLCT-ND
R3, R5: 160; R_0805_2012Metric_Pad1.20x1.40mm_HandSolder; MFG PN RC0805FR-07160RL; Digi PN 311-160CRCT-ND
R6: 1.5k; R_0805_2012Metric_Pad1.20x1.40mm_HandSolder; MFG PN AC0805FR-071K5L; Digi PN YAG3701CT-ND
R7: 680; R_0805_2012Metric_Pad1.20x1.40mm_HandSolder; MFG PN RC0805FR-07680RL; Digi PN 311-680CRCT-ND
R8: 402; R_0805_2012Metric_Pad1.20x1.40mm_HandSolder; MFG PN AC0805FR-07402RL; Digi PN 13-AC0805FR-07402RLCT-ND
R9, R12, R14: 5k; R_0805_2012Metric_Pad1.20x1.40mm_HandSolder; MFG PN RC0805FR-134K99L; Digi PN 13-RC0805FR-134K99LCT-ND
R10, R11, R13: 10k; R_0805_2012Metric_Pad1.20x1.40mm_HandSolder; MFG PN RC0805FR-0710KL; Digi PN 311-10.0KCRCT-ND
R15, R16: 22; R_0805_2012Metric_Pad1.20x1.40mm_HandSolder; MFG PN AC0805FR-0722RL; Digi PN YAG3713CT-ND
R17: 200; R_0805_2012Metric_Pad1.20x1.40mm_HandSolder; MFG PN RC0805FR-07200RL; Digi PN 311-200CRCT-ND
R43: 1K; R_0603_1608Metric_Pad0.98x0.95mm_HandSolder; MFG PN AC0603FR-071KL; Digi PN 311-1KLDCT-ND
SW1: SW_DIP_x04; SW_A6H-4101_OMR; MFG PN A6H-4101; Digi PN 39-A6H-4101-ND
TP1: S6; TestPoint_Pad_D1.5mm
U1: LTC6810IG-2-TRPBF; TSSOP-44_4.4x11mm_P0.5mm; MFG PN LTC6810IG-2#3ZZPBF; Digi PN 505-LTC6810IG-2#3ZZPBF-ND

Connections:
/BB0/B#: J2.4, R1.2; also elsewhere on the board
/BB0/B#+1: J2.3; also elsewhere on the board
/BB1/B#+1: J2.2; also elsewhere on the board
/BB2/B#+1: J2.1; also elsewhere on the board
/BB3/B#+1: J1.5; also elsewhere on the board
/BB4/B#+1: J1.4; also elsewhere on the board
/BB5/B#+1: J1.3, R43.1; also elsewhere on the board
/C0: C1.1, R1.1, U1.16 (C0); also elsewhere on the board
/C1: U1.14 (C1); also elsewhere on the board
/C2: U1.12 (C2); also elsewhere on the board
/C3: U1.10 (C3); also elsewhere on the board
/C4: U1.8 (C4); also elsewhere on the board
/C5: U1.6 (C5); also elsewhere on the board
/C6: U1.4 (C6); also elsewhere on the board
/DRV: Q1.1 (B), U1.33 (DRIVE)
/S0: U1.17 (S0); also elsewhere on the board
/S1: U1.15 (S1); also elsewhere on the board
/S2: U1.13 (S2); also elsewhere on the board
/S3: U1.11 (S3); also elsewhere on the board
/S4: U1.9 (S4); also elsewhere on the board
/S5: U1.7 (S5); also elsewhere on the board
/S6: R43.2, TP1.1, U1.5 (S6)
/extIsoSPI_N: J7.1, J8.2, R16.1
/extIsoSPI_P: J7.2, J8.1, R15.1
A0: R13.1, SW1.4, U1.34 (A0)
A1: R11.1, SW1.3, U1.35 (A1)
A2: R10.1, SW1.2, U1.38 (A2)
ALERT: J3.4, R12.2, U1.19 (GPIO2)
DQ: J4.2, J5.5, J6.1
I2C_SCL: J3.2, R9.2, U1.25 (GPIO4)
I2C_SDA: J3.3, R14.2, U1.20 (GPIO3)
IBIAS: R6.2, U1.40 (SDO(IBIAS))
ICMP: R6.1, R7.2, U1.41 (SDI(ICMP))
IsoSPI_N: C7.1, L1.6, R17.1, U1.36 (CSB(IMA))
IsoSPI_P: L1.4, R8.1, SW1.1, U1.37 (SCK(IPA))
unnamed: C6.1, Q1.2 (C), Q1.4 (C), R4.1
unnamed: C7.2, R8.2
unnamed: C8.1, L1.5
unnamed: D1.2 (A), R3.1
unnamed: D1.1 (K), U1.18 (GPIO1)
unnamed: D2.2 (A), R5.1
unnamed: J1.2, R2.2, R4.2
unnamed: J4.1, J5.1, J6.2
unnamed: L1.1, R16.2
unnamed: L1.3, R15.2
unnamed: R17.2, SW1.8
unnamed: C2.2, R2.1, U1.3 (V+)
unnamed: C5.2, U1.31 (VREF1)
unnamed: C3.2, U1.30 (VREF2)
V-: C1.2, C2.1, C3.1, C4.2, C5.1, C6.2, C8.2, D2.1 (K), J2.5, J3.1, R7.1, R10.2, R11.2, R13.2, U1.1 (V-), U1.21 (V-), U1.22 (V-), U1.23 (V-), U1.24 (V-), U1.26 (DTEN), U1.28 (V-), U1.29 (V-), U1.39 (A3), U1.43 (V-), U1.44 (V-)
VREG: C4.1, J3.5, Q1.3 (E), R3.2, R5.2, R9.1, R12.1, R14.1, SW1.5, SW1.6, SW1.7, U1.27 (ISOMD), U1.32 (VREG)

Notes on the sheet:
ISOSpi Bias setting
Bottom filtering not caught by BalanceSenseBlock
This module was designed as specified in the LTC6811 datasheet.
BMS Temp Sense
E-meter temp sensor low voltage
1: ISOSpi Termintion 2: Address bit 2 3: Address bit 1 4: Address bit 0
Configuration-specific settings switches
Temp Sense Pull-Ups
ISOSpi isolation and filtering


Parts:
C9: 10nF; C_0805_2012Metric_Pad1.18x1.45mm_HandSolder; MFG PN AC0805KRX7R9BB103; Digi PN 311-3174-1-ND
D3: LH R974-LP-1; LED_0805_2012Metric_Pad1.15x1.40mm_HandSolder; MFG PN LS R976-NR-1-0-20-R18; Digi PN 475-LSR976-NR-1CT-ND
D4: 9.1V; D_SOD-523; MFG PN DDZ9696T-7; Digi PN 31-DDZ9696T-7CT-ND
Q2: AO3400A; SOT-23-3; MFG PN AO3400A; Digi PN 785-1000-1-ND
R18: 120; R_0805_2012Metric_Pad1.20x1.40mm_HandSolder; MFG PN RC0805FR-07120RL; Digi PN 311-120CRCT-ND
R19: 33; R_2512_6332Metric_Pad1.40x3.35mm_HandSolder; MFG PN RC2512FK-0733RL; Digi PN 13-RC2512FK-0733RLCT-ND
R20: 1K; R_0603_1608Metric_Pad0.98x0.95mm_HandSolder; MFG PN AC0603FR-071KL; Digi PN 311-1KLDCT-ND
R21: 100; R_0805_2012Metric_Pad1.20x1.40mm_HandSolder; MFG PN RC0805FR-07100RL; Digi PN 311-100CRCT-ND

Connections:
/BB2/B#+1: D4.2 (A), Q2.2 (S), R20.1; also elsewhere on the board
/BB3/B#+1: R18.1, R19.2, R21.2; also elsewhere on the board
/C3: C9.2; also elsewhere on the board
/C4: C9.1, R21.1; also elsewhere on the board
/S3: D4.1 (K), Q2.1 (G), R20.2; also elsewhere on the board
unnamed: D3.2 (A), R18.2
unnamed: D3.1 (K), Q2.3 (D), R19.1

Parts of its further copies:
C10, C11, C12, C13, C14: 10nF; C_0805_2012Metric_Pad1.18x1.45mm_HandSolder; MFG PN AC0805KRX7R9BB103; Digi PN 311-3174-1-ND
D5, D7, D9, D11, D13: LH R974-LP-1; LED_0805_2012Metric_Pad1.15x1.40mm_HandSolder; MFG PN LS R976-NR-1-0-20-R18; Digi PN 475-LSR976-NR-1CT-ND
D6, D8, D10, D12, D14: 9.1V; D_SOD-523; MFG PN DDZ9696T-7; Digi PN 31-DDZ9696T-7CT-ND
Q3, Q4, Q5, Q6, Q7: AO3400A; SOT-23-3; MFG PN AO3400A; Digi PN 785-1000-1-ND
R22, R26, R30, R34, R38: 120; R_0805_2012Metric_Pad1.20x1.40mm_HandSolder; MFG PN RC0805FR-07120RL; Digi PN 311-120CRCT-ND
R23, R27, R31, R35, R39: 33; R_2512_6332Metric_Pad1.40x3.35mm_HandSolder; MFG PN RC2512FK-0733RL; Digi PN 13-RC2512FK-0733RLCT-ND
R24, R28, R32, R36, R40: 1K; R_0603_1608Metric_Pad0.98x0.95mm_HandSolder; MFG PN AC0603FR-071KL; Digi PN 311-1KLDCT-ND
R25, R29, R33, R37, R41: 100; R_0805_2012Metric_Pad1.20x1.40mm_HandSolder; MFG PN RC0805FR-07100RL; Digi PN 311-100CRCT-ND

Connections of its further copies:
/BB0/B#: D14.2 (A), Q7.2 (S), R40.1; also elsewhere on the board
/BB0/B#+1: D12.2 (A), Q6.2 (S), R36.1, R38.1, R39.2, R41.2; also elsewhere on the board
/BB1/B#+1: D10.2 (A), Q5.2 (S), R32.1, R34.1, R35.2, R37.2; also elsewhere on the board
/BB2/B#+1: R30.1, R31.2, R33.2; also elsewhere on the board
/BB3/B#+1: D6.2 (A), Q3.2 (S), R24.1; also elsewhere on the board
/BB4/B#+1: D8.2 (A), Q4.2 (S), R22.1, R23.2, R25.2, R28.1; also elsewhere on the board
/BB5/B#+1: R26.1, R27.2, R29.2; also elsewhere on the board
/C0: C14.2; also elsewhere on the board
/C1: C13.2, C14.1, R41.1; also elsewhere on the board
/C2: C12.2, C13.1, R37.1; also elsewhere on the board
/C3: C12.1, R33.1; also elsewhere on the board
/C4: C10.2; also elsewhere on the board
/C5: C10.1, C11.2, R25.1; also elsewhere on the board
/C6: C11.1, R29.1; also elsewhere on the board
/S0: D14.1 (K), Q7.1 (G), R40.2; also elsewhere on the board
/S1: D12.1 (K), Q6.1 (G), R36.2; also elsewhere on the board
/S2: D10.1 (K), Q5.1 (G), R32.2; also elsewhere on the board
/S4: D6.1 (K), Q3.1 (G), R24.2; also elsewhere on the board
/S5: D8.1 (K), Q4.1 (G), R28.2; also elsewhere on the board
unnamed: D5.2 (A), R22.2
unnamed: D5.1 (K), Q3.3 (D), R23.1
unnamed: D7.2 (A), R26.2
unnamed: D7.1 (K), Q4.3 (D), R27.1
unnamed: D9.2 (A), R30.2
unnamed: D9.1 (K), Q5.3 (D), R31.1
unnamed: D11.2 (A), R34.2
unnamed: D11.1 (K), Q6.3 (D), R35.1
unnamed: D13.2 (A), R38.2
unnamed: D13.1 (K), Q7.3 (D), R39.1

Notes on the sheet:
Balance Block


Board: 2 copper layers, 183.2 x 49.9 mm, 89 parts (0 on the bottom side), 63 nets.

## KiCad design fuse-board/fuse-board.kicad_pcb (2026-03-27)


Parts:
F1, F2, F3, F4, F5, F6, F7, F8, F9: 3568; Fuseholder_Blade_Mini_Keystone_3568; MFG PN 3568; Digi PN 36-3568-ND
H1: MountingHole M3; MountingHole_3.2mm_M3
J1, J2: 74651173R; MFG PN 74651173R; Digi PN 732-74651173RCT-ND
J3: 1053141106; Molex_Nano-Fit_105314-xx06_2x03_P2.50mm_Horizontal; MFG PN 1053141106; Digi PN WM16908-ND
J4: ATM15-12PA-BM04; ATM15-12PX-BMXX; MFG PN ATM15-12PA-BM04; Digi PN 889-3307-ND

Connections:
/12V_In: F1.1, F2.1, F3.2, F4.2, F5.2, F6.2, F7.1, F8.1, F9.1, J1.1
/Inverter: F9.2, J3.6
/PEB: F7.2, J3.1, J3.4
/Shutdown: F8.2, J3.5
/TBB: F4.1, J4.3
/TB_Fan_A: F1.2, J4.6
/TB_Fan_B: F2.2, J4.5
/TB_Fan_C: F3.1, J4.4
/Telemetry: F6.1, J4.1
/VCU: F5.1, J4.2
GND: J2.1, J3.2, J3.3, J4.7, J4.8, J4.9, J4.10, J4.11, J4.12

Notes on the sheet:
10A ATM
5A ATM
No return for PEB because the return is on the PEB. Pin 1 gets PEB 12V for use with the 12V measuring point


Board: 2 copper layers, 73.7 x 55.9 mm, 14 parts (0 on the bottom side), 11 nets.

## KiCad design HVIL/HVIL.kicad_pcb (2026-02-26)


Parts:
J9: TS+/TS-; Molex_Nano-Fit_105309-xx02_1x02_P2.50mm_Vertical
J10: HVIL+/HVIL-; Molex_Nano-Fit_105309-xx02_1x02_P2.50mm_Vertical
PS1: TMR_3-7211WIR; Converter_DCDC_TRACO_TMR3-24xxWIR_48xxWIR_72xxWIR_THT; PARTREV July 4, 2024
R1: 294k; R_0805_2012Metric_Pad1.20x1.40mm_HandSolder
R2: 10k; R_0805_2012Metric_Pad1.20x1.40mm_HandSolder
R3: 15k; R_0603_1608Metric_Pad0.98x0.95mm_HandSolder
R4: 10k; R_0603_1608Metric_Pad0.98x0.95mm_HandSolder
U1: MCP6004; SOIC-14_3.9x8.7mm_P1.27mm

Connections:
/TS+: J9.1, PS1.2 (+VIN(VCC)), R1.2
HVIL+: J10.1, U1.1
HVIL-: J10.2, PS1.6 (+VOUT), R3.1, U1.4 (V+)
unnamed: R1.1, R2.2, U1.3 (+)
unnamed: R3.2, R4.1, U1.2 (-)
TS-: J9.2, PS1.1 (-VIN(GND)), PS1.7 (-VOUT), R2.1, R4.2, U1.11 (V-)

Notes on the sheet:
(TS+)*(1/30)
TS+ Max: 150V


Board: 2 copper layers, 8 parts (0 on the bottom side), 6 nets.

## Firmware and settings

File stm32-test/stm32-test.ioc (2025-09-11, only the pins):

Mcu.UserName=STM32G441KBTx
PA11.Signal=FDCAN1_RX
PA12.Signal=FDCAN1_TX
PA13.Signal=SYS_JTMS-SWDIO
PA14.Signal=SYS_JTCK-SWCLK
PA2.Signal=USART2_TX
PA3.Signal=USART2_RX
PA4.Signal=SPI1_NSS
PA5.Signal=SPI1_SCK
PA6.Signal=SPI1_MISO
PA7.Signal=SPI1_MOSI
PA8.Signal=I2C2_SDA
PA9.Signal=I2C2_SCL
PB3.Signal=SYS_JTDO-SWO
PF0-OSC_IN.Signal=RCC_OSC_IN
PF1-OSC_OUT.Signal=RCC_OSC_OUT

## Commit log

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2025-08-30 stm32-test progress; added global symbol & footprint libraries
    [stm32-test.kicad_pcb, stm32-test.kicad_sch]
2025-08-31 not really sure if I changed anything here
    [stm32-test.kicad_pcb]
2025-09-11 save (not quite sure what the diff is?); update stm32 project version; add gerbers
    [stm32-test-B_Cu.gbr, stm32-test-B_Mask.gbr, stm32-test-B_Paste.gbr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]
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2025-11-07 Fixed addressing and removed A-PINS on config switches
    [TempSensor.kicad_sch]
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2025-11-20 Revert "bms busbar board start"
    This reverts commit c45fd83070c58d8eb2b3658edb9c526345643df1.
    [BMS Module Board.kicad_pcb, BMS Module Board.kicad_sch, BMS Module Board.step]
2025-11-20 BMS
    fixed errors
    trace width to 0.254
    [BMS.kicad_pcb, BMS.kicad_sch]
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2025-11-20 TMPDev Board
    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
    [TMPDev.kicad_pcb]
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2025-11-20 Hide MFG Labels in STM32-test
    Hide purple MFG labels in STM32-test
    [stm32-test.kicad_sch]
2025-11-20 rough draft of mcu design blocks
    barebones templates for design blocks
    [dash-screen-mcu.kicad_pcb, dash-screen-mcu.kicad_sch, peripheral-mcu.kicad_pcb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]
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2025-11-20 add CAN to design blocks + fix g441kb power
    [STM32G441KBTx.kicad_sch]
2025-11-20 Fix power for G473RCTx
    [STM32G473RCTx.kicad_sch]
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2025-11-22 BMS
    updated BMS schematic with new global tags
    [BMS.kicad_sch, BalanceSenseBlock.kicad_sch]
2025-11-22 redo G441KB with VDDA net + create F4
    [STM32F446RETx.kicad_pcb, STM32F446RETx.kicad_sch, STM32G441KBTx.kicad_sch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]
2025-11-22 fix G441KB caps
    [STM32G441KBTx.kicad_sch]
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2025-11-23 TMPDev Board
    - fixed schematic design to fit global label criteria
    - made schematic neater
    [TMPDev.kicad_pcb, TMPDev.kicad_sch]
2025-12-01 fix footprint for ferrite bead
    [STM32F446RETx.kicad_sch, STM32G441KBTx.kicad_sch, STM32G473RCTx.kicad_sch]
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2025-12-02 BMS
    fixed errors with power flags
    [BMS.kicad_pcb, BMS.kicad_sch, BalanceSenseBlock.kicad_sch]
2025-12-16 TMPDev
    update the PCB with the mounting holes
    [TMPDev.kicad_pcb]
2025-12-20 TMPDev
    Further Rounded Corners
    Nanofit on bottom side
    moved mounting holes
    realigned drawings
    resized board
    changed mounting holes from m2 to m3
    [TMPDev.kicad_pcb]
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2026-01-05 use snapeda cad files for stlinkv3-mods
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2026-01-08 Update BMS.kicad_sch
    fixed schematic
    added power flags
    [BMS.kicad_sch]
2026-01-08 BMS
    -Slightly Modified recent 6810 symbol changes
    -Fixed wiring
    [BMS.kicad_sch]
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2026-01-10 fixed files
    [TMPDev.kicad_sch, TempSenseBoard.kicad_sch]
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2026-01-16 fixed 5V linear regulator and added 12->3.3V one
2026-01-17 Update chargingboard.kicad_sch
    Made more physical connections, started connecting transceiver
    [chargingboard.kicad_sch]
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2026-01-22 small updates (erc fixes)
    small updates
    [chargingboard.kicad_sch, screen_architecture.kicad_sch]
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2026-01-24 bms changes made
    - added fps connectors and pull ups
    - need to fix traces width still and clean up
    [BMS.kicad_pcb, BMS.kicad_sch]
2026-01-25 fixed nanofit 1054301202 footprint
    added molex nanofit 1054301202 to footprint library
2026-01-25 some schematic changes made
    -fixed emeter sensor wiring
    -sw2 symbol fixed
    -redid cell voltage fpc connector wiring
    - fixed A3 pin
    - removed r3
    [BMS.kicad_pcb, BMS.kicad_sch]
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2026-01-31 changes made
    -Added ltc6810 to fs4 symbol library
    - fixed erc error
    - fixed symbol fields
    - changed connector symbols
    - fixed LTC6810 and HM2113ZNL library link
    [BMS.kicad_pcb, BMS.kicad_sch, BalanceSenseBlock.kicad_sch]
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2026-02-01 changes
    - replaced 5019510550 connector to 512810598
    - schematic cleanup
    - added new connector to footprint library
    [BMS.kicad_pcb, BMS.kicad_sch]
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2026-02-04 footprints and fixed sizing
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2026-02-05 busboard progress (possibly wrong connector)
    [BMS Busbar Board.kicad_pcb]
2026-02-05 finalschemfixesp1
    fixed more schem issues
    [chargingboard.kicad_sch, screen_architecture.kicad_sch]
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2026-02-06 Removed unused footprints, symbols and fixed library paths
2026-02-06 Fixed wrong footprint assignments and removed unused symbols
2026-02-07 pcb wired (drc errors)
    [BMS Busbar Board.kicad_pcb, BMS Busbar Board.kicad_sch]
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2026-02-09 layout
    added dimensions and made hvlv line dashed
    [BMS.kicad_pcb, BMS.kicad_sch]
2026-02-09 Fixed minor silkscreen issues
    [BMS.kicad_pcb]
2026-02-09 fixed emeter nanofit height
    [BMS.kicad_pcb]
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2026-02-09 violation fixes (still needs screw holes)
    [BMS Busbar Board.kicad_pcb]
2026-02-10 Update BMS.kicad_pcb
    some isospi trace improvement
    fixed via sizes for trace widths of 20 mils
    [BMS.kicad_pcb]
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2026-02-22 fixed merge conflict
    fixed merge
    [chargingboard.kicad_sch]
2026-02-23 more schem fixes for rev
    more schem fixes for rev - added footprints to steering, no more pwr flags, better labels
    [chargingboard.kicad_sch, screen_architecture.kicad_sch]
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2026-02-24 top right screw hole added
    -MP pins throwing DRC errors
    [BMS Busbar Board.kicad_pcb]
2026-02-26 Fixed screw posistion and deleted connectors
    [BMS Busbar Board.kicad_pcb]
2026-02-26 more erc fix
    title says it all
    [chargingboard.kicad_sch, screen_architecture.kicad_sch]
2026-02-26 VCU Board Rev. 1.5
    * VCU PCB and Schematic
    Upload of current VCU pcb and schematic.
    * VCU Schematic Update
    Documented schematic in more detail. Added and removed certain components based on feedback.
    * VCU Documentation Update
    footprint, annotations, and more!
    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
    [IMU.kicad_sch, MCU.kicad_sch, Shutdown_LEDS.kicad_sch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]
2026-02-26 Peripheral Board Rev 1.1 (Order 1) (#10)
    * Add project template
    Needs review, focusing on PCB layout rules
    * Added STM32 and old blocks
    Added STM 32 but didnt connect anything and added over old blocks from the old schematic
    * Added wheel speed sensor symbol
    * Connected wheel speed sensor and and strain gauge to mc
    * Connected the rest of the sensors
    * updated libraries
    * Updated to do list for the schematic with questions
    * Annotated things that need to be done this weekend
    -standardized sensors and other symbols
    -added power supplies
    -
    * Changes Connectors and Linear Regulator and Sensors
    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
    [FS_KiCad_TEMPLATE.kicad_pcb, FS_KiCad_TEMPLATE.kicad_sch, peripheral-boards.kicad_pcb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]
2026-02-26 Merged main into BMS, Squashed commit of the following:
    commit be147252164e59999344f17533bd10e446f5820c
    Author: ninalane1 <nllane@ucsc.edu>
    Date: Thu Feb 26 13:57:40 2026 -0800
    Peripheral Board Rev 1.1 (Order 1) (#10)
    * Annotated things that need to be done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
    [FS_KiCad_TEMPLATE.kicad_pcb, FS_KiCad_TEMPLATE.kicad_sch, IMU.kicad_sch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]
2026-02-26 Bms Rev 1.1 (Order 1) (#8)
    * prototype BMS Temp Sensor Board
    * full prototype schematic
    * Fixed addressing and removed A-PINS on config switches
    * attempt temp sensor tester board
    * TMP1075 Dev Board
    * BMS board
    * BMS
    * BMS
    * TMPDev Board
    * TMPDev Board
    * Update BMS.kicad_pcb
    * BMS
    * TMPDev Board
    * BMS
    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
    [BMS.kicad_pcb, BMS.kicad_sch, BalanceSenseBlock.kicad_sch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]
2026-02-26 Steering wheel Rev 1.2 (Order 1) (#13)
    * Set up steering wheel directory
    * power, can, and bridgetek drivers on steering wheel board schematic
    * began work on MCU schematic sheet
    * MCU page of steering wheel schematic
    * added priority encoder for rotary dials on steering wheel to library
    * backlight circuit added to datasheet
    * added some notes
    * ribbon cable connection added
    * started work on dial encoders
    * page numbers added to datasheet references
    * encoders added to steering wheel schematic
    * added footprint for inductor on dash backlight driver
    * added power flag to fix ERC error
    * added notes
    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
    [MCU.kicad_sch, display.kicad_sch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]
2026-02-26 Power Electronics Board Schematic rev 1 (#14)
    * Power Electronics Board Version 1
    This is the first revision of the power electronics board schematic. Layouts have not been done yet, awaiting review.
    * Update Power Electronics Board.kicad_sch
    * Update Power Electronics Board.kicad_pro
    * Fixing boxes not showing up
    * Power Electronics Board Schematic Update 1.1
    Fixed 5V Isolation, added gate resistor and pull down resistor for CR2 mosfet,
    have not done yet: checking the max and min of 3V reference (U2) and changing it to one relay instead of two, also have not sourced connectors
    waiting on: Cole to push 5V dcdc schematic block, will put back onto board after doing so
    * cherry pick Sym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
    [Power Electronics Board.kicad_pcb, Power Electronics Board.kicad_sch]
2026-02-26 Tractive battery board Rev 1.2 (#15)
    * TB current progress
    * MCU Design Block + Shutdown Relays
    * Shutdown Relay Drivers, Power Blocks, E-meter
    * Precharge Relay, Board Mounted E-meter, wiring cleanup
    * Test Points
    * small tweaks
    * Current Sensor
    * Shutdown driver relays and diodes fixed + some diff amp work
    * TBB V1
    * changed mosfets -> relay drivers, E-meters fixed, BMS shutdown WIP
    * minor tweaks
    * small corrections
    * Shutdown LED logic fixed
    * more small changes
    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
    [Current_Sensors.kicad_sch, HVIL.kicad_pcb, HVIL.kicad_sch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]
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2026-03-01 some more fixes
    some more fixes
    [chargingboard.kicad_sch, screen_architecture.kicad_sch]
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2026-03-09 TempSenseBoard
    -Needs to finish wiring
    -redo pcb addressing
    [TempSenseBoard.kicad_pcb, TempSenseBoard.kicad_sch]
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2026-03-27 Fuse board (#24)
    * fuse board v1.0
    * rev 1.1 with mini-fit sr
    * v1.2 with ring terminal studs
    * v1.3 filled out symbol fields and improved traces
    * v1.4 added note for 12VMP, fixed silkscreen title, fixed chud trace
    [fuse-board.kicad_pcb, fuse-board.kicad_sch]
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2026-03-31 whitespace fixes
    whitespace fixes
    [chargingboard.kicad_sch, screen_architecture.kicad_sch]
2026-03-31 some whitespaces fixes
    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
    [chargingboard.kicad_sch, screen_architecture.kicad_sch]
2026-04-01 more whitespace fixes
    more whitespace fixes
    [chargingboard.kicad_sch, screen_architecture.kicad_sch]
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2026-04-02 step file with connectors
    step file with connectors
    [chargingboard.kicad_pcb]
2026-04-02 fixed step
    fixed step
    [chargingboard.f3d, chargingboard.kicad_pcb]
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2026-04-04 Rev 2.0
    Added Potentiometer to non inverting pin for LV battery op amp
    changed 24.9k resistor to something more standard
    Updated both schematic and layout
    [Power Electronics Board.kicad_pcb, Power Electronics Board.kicad_sch]
2026-04-04 Rev 2.1
    For some reason on my end my changes werent there, so im not sure if my changes are on github either, so i redid them and am pushing it back onto git
    [Power Electronics Board.kicad_pcb, Power Electronics Board.kicad_sch]
2026-04-04 Rev 2.1.1
    just sum light trace edits nun much
    [Power Electronics Board.kicad_pcb]
2026-04-04 Rev 2.2
    Finished Rev 2 layout, mostly worried about HV side. Need to add more silk screen comments for connectors
    [Power Electronics Board.kicad_pcb, Power Electronics Board.kicad_sch]
2026-04-04 Rev 2.3
    Updated schematic's comments, added labels for connectors
    [Power Electronics Board.kicad_pcb, Power Electronics Board.kicad_sch]
2026-04-04 fixed addresses
    [TempSenseBoard.kicad_pcb, TempSenseBoard.kicad_sch]
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2026-04-04 fixes
    fixes
    [chargingboard.kicad_pcb, chargingboard.kicad_sch, screen_architecture.kicad_sch]
2026-04-04 more fixes
    more fixes
    [chargingboard.kicad_sch, screen_architecture.kicad_sch]
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2026-04-04 test fit in CAD with 2 temp sensors and 2 connectors
    [TempSenseBoard.kicad_pcb]
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2026-04-09 V1.3: SPI pins corrected + TPs, IMD Delay data table correction
    [Tractive_Battery_Board.kicad_pcb, Tractive_Battery_Board.kicad_sch]
2026-04-09 STLINK TX/RX Fix
    [Tractive_Battery_Board.kicad_pcb, Tractive_Battery_Board.kicad_sch]
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2026-04-09 layout pre connector change
    layout pre connector change
    [chargingboard.kicad_pcb, chargingboard.kicad_sch, screen_architecture.kicad_sch]
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2026-04-10 ERC fixes + HVIL circuit corrections.
    [Current_Sensors.kicad_sch, HVIL.kicad_sch, Tractive_Battery_Board.kicad_pcb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]
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2026-04-12 fixing drc
    fixing drc
    [chargingboard.kicad_pcb, chargingboard.kicad_sch]
2026-04-12 Rev 2.4
    Confirmed with @fezboy that layout + schematic were OK. Added 3d models for big important space-relevant components. Still waiting on the OK from @victorkalastirsky mechanically
    [Power Electronics Board.kicad_pcb, Power Electronics Board.kicad_sch, Power Electronics Board.step]
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2026-04-12 drc fixes
    drc fixes
    [chargingboard.kicad_pcb, chargingboard.kicad_sch]
2026-04-12 fixed label
    fixed label
    [chargingboard.kicad_pcb]
2026-04-12 fixed edge cut drc errors
    [BMS Busbar Board.kicad_pcb, BMS Busbar Board.step]
2026-04-12 separation converted from mils to mm
    7.62 mm was written as 300 mils before
    [chargingboard.kicad_pcb]
2026-04-12 Rev 2.5.1
    More layout changes to fit into inverter box. @victorkalastirsky has 90% confirmed that the layout is okay, worried about bend radiuses for the high current connector wires. I'm worried about the spa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
    [Power Electronics Board V2.5.step, Power Electronics Board.kicad_sch]
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2026-04-13 BMS rev 2 changes
    - I changed pin25 to GPIO4, and replaced the GPIO1 on the temp sense connector and temp sense pullups to GPIO4.
    - I added the new busbar connectors
    What would we do with the GPIO1 pin? Add the same led that was on GPOI4 previously?
    [BMS.kicad_pcb, BMS.kicad_sch, BMS.step]
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2026-04-14 Rev 2.6
    K2 (AZ2150-1A-12DEF) had the wrong pin numbers, connecting high current traces to the coils. Renumbered pin numbers on footprint, and fixed layout to account for the change.
    [Power Electronics Board.kicad_pcb, Power Electronics Board.kicad_sch]
2026-04-14 R2.1 Apply sch. changes to PCB Layout
    2nd CAN Transceiver (U3)
    Additional Temp Sense Connector
    [Current_Sensors.kicad_sch, HVIL.kicad_sch, Shutdown Logic.kicad_sch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]
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2026-04-14 silkscreen fix and pretty traces
    [Tractive_Battery_Board.kicad_pcb]
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2026-04-15 Revert "Layout done, missing documentation"
    This reverts commit c3ceebc9681f6c0cf3131b0774409dfcb98ecb72.
    [TempSenseBoard.kicad_pcb]
2026-04-15 Reapply "Layout done, missing documentation"
    This reverts commit 1e948bdb4d8a40a0e2bb55c414871b86708bd90c.
    [TempSenseBoard.kicad_pcb]
2026-04-15 Board Layout
    Accidentally pushed to TBB, reverted changes and pushed here
    [TempSenseBoard.kicad_pcb]
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2026-04-17 minor trace changes, waiting on BMS to be fixed
    [TempSenseBoard.kicad_pcb]
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2026-04-17 R2.1.1: Correct Ordering info for 1mm FPC Conns
    [BMS.kicad_sch]
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2026-04-22 Fix 2,3 pin SMD Nanofit 3d model association
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2026-04-29 remove old conflicting BMS: '9463091 - Bms Rev 1.1 (Order 1) (#8)'
    [BMS.kicad_pcb, BMS.kicad_sch, BalanceSenseBlock.kicad_sch]
2026-04-29 updated minor fixes for ordering
    [TempSenseBoard.kicad_pcb, TempSenseBoard.kicad_sch]
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2026-05-01 added fixes
    addes fixes
    [chargingboard.kicad_pcb]
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2026-05-04 BMS Rev3.0.0: Fix balance block: use NMOS, use datasheet recommended setup
    [BMS.kicad_pcb, BMS.kicad_sch, BalanceSenseBlock.kicad_sch]
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2026-05-15 layout fixes
    [BMS.kicad_pcb, BMS.kicad_sch]
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2026-05-16 Rev 2.6
    Fixed CRITICAL OP AMP INPUT ISSUE, did not change layout of big components
    [Power Electronics Board-B_Cu.gbr, Power Electronics Board-B_Mask.gbr, Power Electronics Board-B_Paste.gbr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]
2026-05-16 Rev 2.1.2: Current sensor fixes - buffer flipped, instrumentation amplifier symbol + output signal corrections
    [Current_Sensors.kicad_sch]
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2026-05-18 New revision changes
    Added reference voltage to instrumentation amplifier for current sensor.
    Changed 3.3v to 5v on instrumentation amplifier.
    [Current_Sensors.kicad_sch, HVIL.kicad_sch, Shutdown Logic.kicad_sch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]
2026-05-18 Added clamping and fixed redundancy
    Adding a 3.4v zener diode and removed op amp.
    [Current_Sensors.kicad_sch, Tractive_Battery_Board.kicad_pcb]
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2026-06-03 PWM on Pin 26 (previously unused)
    PWM on Pin 26 (previously unused)
    [chargingboard.kicad_pcb, chargingboard.kicad_sch, screen_architecture.kicad_sch]
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
